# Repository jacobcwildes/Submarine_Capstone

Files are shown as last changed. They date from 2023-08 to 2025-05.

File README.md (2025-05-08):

# 2023 Submarine Capstone
This GitHub repo will go over the entire process of making a submersible ROV using custom PCBs, and almost entirely 3D printed hull pieces. This project was borne from ideas pooled by Dyllon Dunton and Jacob Wildes to fulfill a senior Capstone at the University of Maine. The end goal of this project is to have a submersible drone which can be operated by human input, and all relevent telemetry (i.e. forward velocity, and depth) will be displayed to the user. The bulk of the project was split into two parts: Dyllon Dunton completing the submarine portion and all PCB layouts, and Jacob Wildes completing the controller and all of the startup networking. Additionally, as Jacob progresses with his undergrad thesis work, eventually the need for human input will dwindle. Instead, a neural network will randomly patrol an area and as things appear (i.e. fish, lakegrass, etc.) that object will be outlined, and if desired, saved to local memory. By using IMU telemetry, the submarine should not continuously patrol the same route, though currents and other unconsidered elements may alter this. However, that is a non-issue because of the nature of the environment. Aquatic life is not constrained to the same location at all times, so even if it were in the same area twice, there may be something there that was not before.

# Photos



<div style="display: flex; gap: 10px;">
    
    
</div>

## Index
[STL Docs](https://github.com/jacobcwildes/Submarine_Capstone/tree/main/manufacturing_stls/README.md)

[PCB Docs](https://github.com/jacobcwildes/Submarine_Capstone/blob/main/pcb_files/README.md)

[Node Docs](https://github.com/jacobcwildes/Submarine_Capstone/tree/main/ros2_ws)

[STM Docs](https://github.com/jacobcwildes/Submarine_Capstone/tree/main/stm32_ws)

## Software Requirements
- Machine must be running Ubuntu 20.04.5 LTS
- ROS2 Foxy 
    - Can be installed using these [directions](https://docs.ros.org/en/foxy/Installation/Ubuntu-Install-Debians.html)
- CycloneDDS
    - Can be installed by doing the following: ```sudo apt install ros-foxy-rmw-cyclonedds-cpp```
    - This either needs to be sourced each time by running ```export RMW_IMPLEMENTATION=rmw_cyclonedds_cpp``` or automatically by adding it to the bashrc file.
- Docker Engine (optional - useful if a premade image is desired)
- OpenCV - the latest version is OK
    - Install can be found [here](https://docs.opencv.org/4.x/d7/d9f/tutorial_linux_install.html)
    - Note that Jacob highly recommends going directly to detailed install process. The quickstart makes it easy to make a mistake!
- Python 3.8.10
- Pyserial - latest version is OK. Can be installed with:
python3 -m pip install pyserial
 - STM32CubeMX or STM32CubeIDE
    - CubeMX is fine if you are comfortable with Makefiles. Otherwise, use the IDE which makes flashing the board as easy as pressing a play button 

## Hardware Requirements
- 2 Raspberry Pi 4Bs were used with 8 GB of RAM (one for the submarine, one for the controller). It may be possible to achieve success with less, but bear in mind there is much OpenCV work being done on the controller side to run the display.
- STM32 Nucleo-L4R5ZI (For submarine)
- STM32 Nucleo-L452RE-P (For controller)
## Installation

Since this is a large project, installs can sometimes get pretty messy. For example, ROS2 uses ```colcon build``` to prepare an executable. This is very handy and incredibly powerful. _However_ there isn't any sane way to rein in what colcon attemps to build, and surprise surprise, when colcon expects python and runs across C source code, it has no idea what to do. To alleviate this, we have made subdirectories called ros2_ws (which acts as our root ROS2 folder for all nodes) and stm32_ws (which acts as the root STM workspace for both the controller and submarine).

To actually download/install, follow these steps:

## Pi Setup

As per usual, it is never a super easy process to set anything up. To flash the Raspberry Pi Jacob opted to use the official [Raspberry Pi Imager](https://www.raspberrypi.com/software/). This tool allows for easy flashing of SD cards. However, when perusing the options to install the Ubuntu environment, as of the date of flashing (7/23), there was no 64-bit Ubuntu 20.04.5 LTS desktop option. The only option was a server version. Without much other option, the server option works as a good enough base. In Jacob's experience, even if a Wi-Fi setting is given in the imager, it still fails to find a network connection when the server is booted (note that the server version is only a command line). 

*NOTE*: For easiest plug and play ability, use the username "controller" for the controller and "ubuntu" for the submarine. If these are not followed, the systemd files will have to be modified so that the absolute paths line up. Systemd does not yet have access to the $USER environment variable so it cannot be flexible unfortunately.

In order to solve these networking woes, we need to modify our netplan file. This can be done by running 
```sudoedit /etc/netplan/<filename>.yaml``` 
where "filename" is the first entry that shows up when you hit tab a couple times. In Jacob's case it was 50-cloud-init.yaml, though your mileage may vary. 
Once inside the document, you will want to paste the following into it:
```bash

network:
    version: 2
    renderer: networkd
    ethernets:
        eth0:
            dhcp4: false
            critical: true #Tell netplan this is important and should be done early in setup
            addresses:
                - <your_desired_address>/24
    version: 2
    wifis:
        wlan0:
            optional: true
            access-points:
                <Wi-Fi_name>:
                    password: <your_password>
            dhcp4: true
            dhcp4-overrides:
                use-dns: false
            critical: true #Tell netplan this is important and should be done early in setup
            nameservers:
                addresses: [<Your ISP DNS here>] #Note this changes per ISP, can be easily looked up. Google also has development DNSes as well at 8.8.8.8 and 8.8.4.4
            routes:
                - to: 0.0.0.0/0 #All possible IPv4 addresses. Wildcard route for any unmatched traffic 
                  via: 192.168.1.1 #Gateway IP Address
                  metric: 100 #Give a priority. Lower metric means higher priority

```
"your_desired_address> should be something like 192.168.1.X, but it can be whatever you like. This makes it so when we attach both Pis together, they have a static IP and can immediately talk to each other. "Wi-Fi_name" is the name of your wireless network. "your_password" is the password of your wireless network. 

The eth0 option is needed because by default the Pi will not pick up the ethernet connection. This is probably because the gnome desktop is installed over top of the server installation, and the GUI functionality does not work.

Once that is done, it is time to apply those changes. Run the following:
```bash
sudo netplan generate && sudo netplan apply
```
This command will take some time, but afterward the Pi should be attached to the web!

## Getting the Ubuntu Desktop
Now that the Pi is on the web, it is important to actually get our GUI installed. To do so run the following:
```bash
sudo apt update && sudo apt upgrade -y
```
```bash
sudo apt install sudo apt install ubuntu-desktop -y && sudo reboot
```
Once the desktop is installed, you will be ready to download/run the nodes!

NOTICE: If you install SLiM, the boot process will be anywhere from 4-5 seconds faster. This also poses a risk of interfering with netplan since the GUI will also try to interface with wireless networks. Should you have installed SLiM, use the GUI to connect to Wi-Fi and comment out the wlan0 section of the netplan.

Note: This must be done twice, once for each Pi. Make very sure that the designated IP address for the eth0 port is not the same on both Pis! It absolutely will not work if both Pis have the same. 

## Software Install
1)
```bash
git clone https://github.com/jacobcwildes/Submarine_Capstone.git
```

3)
```bash
cd Submarine_Capstone/ros2_ws
```

4)
```bash
source /opt/ros/foxy/setup.bash
```

6) Note: **Before** running this step, make sure you are NOT in the ros2_ws/src directory. When colcon builds it makes 3 directories. An install, a build, and a log directory. When we go to run a ROS2 node, we first source the bash script in the install folder. The way Jacob has set up the launchfiles, the node WILL fail if the folders are not properly built.
```bash
colcon build
```

8) Once the build is finished
```bash
source install/setup.bash
```

## Creating a Mountpoint for the USB drive

First, make sure that the USB drive you are trying to flash is in FAT32 type. It can be any size as we are only saving desired screenshots to the drive. Once it is formatted (if necessary at all), plug into the Pi and do the following:

1)
```bash
sudo fdisk -l
```
Find the drive that corresponds to your drive. I found it is easiest to identify by size and type. If you know it is FAT32 and is 16GB in size, you can deduce the device mountpoint. In our case, it was "/dev/sdb1"

2) Next we need to get the UUID of the drive by running the following:
```bash
sudo ls -l /dev/disk/by-uuid/
```
Look for the entry that corresponds to your mountpoint. For example, our UUID was "A097-2639"

3) Now we need to make a folder for the USB to mount to
```bash
sudo mkdir /mnt/usb
```
The folder name can be whatever you want, but for simplicity I went with "usb"

4) Now we're going to modify the fstab file so that the drive will _always_ be mounted to the "/mnt/usb" partition
```bash
sudo nano /etc/fstab
```

5) Add the following line to the end
```bash
UUID=A097-2639 /mnt/usb vfat uid=${USER},gid={USER} 0 0
```
UUID is your drive ID, and ${USER} is your system username. 

6) Reboot or immediately test by running:
```bash
sudo mount -a
```
If all went well, the drive will be mounted to "/mnt/usb"!
## Flashing STM Boards

_Installing with STM32CubeIDE_

First, make sure that the IDE is installed on your computer. It can be installed from [STM's website](https://www.st.com/en/development-tools/stm32cubeide.html).
Once the software is installed, open the IDE and navigate first to the controller_stm.ioc which can be found in ```Submarine_Capstone/stm32_ws/controller_stm```. Once the project is open in the IDE, the next step is to press the green play button on the top of the screen to flash the Nucleo-L452RE-P with the controller program as shown below
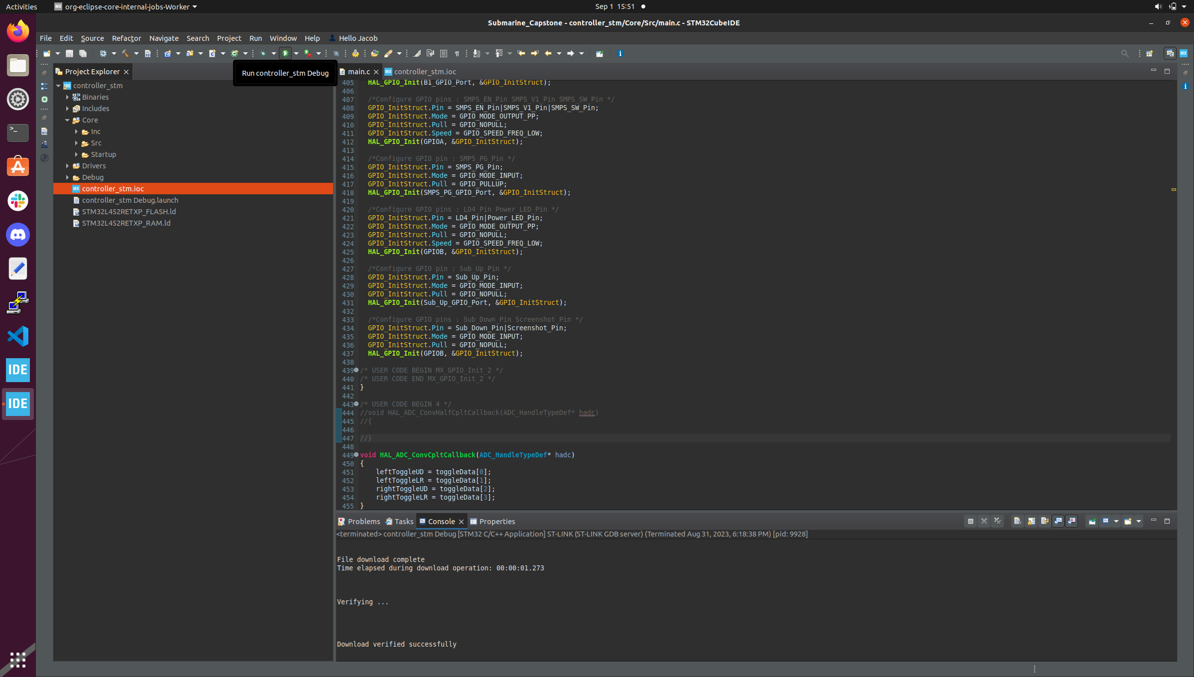
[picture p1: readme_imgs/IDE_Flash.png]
STM32CubeIDE Steps


You will know when the program flashes when the LED next to the USB connection illuminates green.

Repeat this step for the submarine by navigating to ```Submarine_Capstone/stm32_ws/submarine_stm/Submarine_MicroController```

_Installing with STM32CubeMX_

Installing with the CubeMX is a little bit different than the IDE - it is significantly more involved, but for some is the preferred method (especially if your device does not support the IDE). 

First, make sure that you have arm-none-eabi installed on your system. This step can be an absolute nuisance, so the steps are listed below:

1) Check to make sure that you don't have any arm libraries lurking that could foul the download:
```bash
sudo apt remove gcc-arm-none-eabi
```
2) Download the [arm-none-eabi-gcc tarball](https://developer.arm.com/downloads/-/gnu-rm). Note this guide is specifically for Linux. MacOS and Windows mileage will vary from this  guide.

3) Unpack the tarball into some sort of directory. In this case we arbitrarily chose /usr/share
```bash
sudo tar xjf gcc-arm-none-eabi-YOUR-VERSION.bz2 -C /usr/share/
```
"YOUR-VERSION" is whatever version ARM happens to have released at the time

4) Create symlinks from the install folder to the /usr/bin folder like so:
```bash
sudo ln -s /usr/share/gcc-arm-none-eabi-YOUR-VERSION/bin/arm-none-eabi-gcc /usr/bin/arm-none-eabi-gcc 
sudo ln -s /usr/share/gcc-arm-none-eabi-YOUR-VERSION/bin/arm-none-eabi-g++ /usr/bin/arm-none-eabi-g++
sudo ln -s /usr/share/gcc-arm-none-eabi-YOUR-VERSION/bin/arm-none-eabi-gdb /usr/bin/arm-none-eabi-gdb
sudo ln -s /usr/share/gcc-arm-none-eabi-YOUR-VERSION/bin/arm-none-eabi-size /usr/bin/arm-none-eabi-size
sudo ln -s /usr/share/gcc-arm-none-eabi-YOUR-VERSION/bin/arm-none-eabi-objcopy /usr/bin/arm-none-eabi-objcopy
```
Note: These symlinks may or may not be necessary. On some systems Jacob has worked with, the symlinks were a problem. In other systems, they were not. For safety's sake it's easy enough to just create them and prevent headache later.

5) ARM in its infinite wisdom does not give all the necessary dependencies in its README.txt, but these dependencies served well for this project:
```bash
sudo apt install libncurses-dev
sudo ln -s /usr/lib/x86_64-linux-gnu/libncurses.so.6 /usr/lib/x86_64-linux-gnu/libncurses.so.5
sudo ln -s /usr/lib/x86_64-linux-gnu/libtinfo.so.6 /usr/lib/x86_64-linux-gnu/libtinfo.so.5
```
Note: The libncurses.so.6/.so.5 may not be the same at a later date.

6) Check to make sure that the arm-none-eabi was properly installed:
```bash
arm-none-eabi-gcc --version
arm-none-eabi-g++ --version
arm-none-eabi-gdb --version
arm-none-eabi-size --version
```
Make should be installed on your system since OpenCV is a prerequisite for this system to work, but just in case it isn't:
```bash
sudo apt update && sudo apt install make
```
Next, navigate to ```Submarine_Capstone/stm32_ws/submarine_stm/Submarine_MicroController```. This is where the Makefile is.
Run
```bash
make -j4
```
Once the build is complete, run the following:
```bash
cp BINARY_PATH /media/${USER}/BOARD_NAME/
```
BINARY_PATH will be filled in soon, BOARD_NAME is the name of the board when it is plugged into the computer.

If all worked well, the board will be successfully flashed!

Thankfully, once a board is flashed it stays flashed. Once the board is powered, it will immediately begin whatever program is on it.

## Setting up ROS2 to run on boot
This step took a huge amount of debug. Crontab does not play well with ROS2, so Jacob had to opt for systemd instead. Within the Submarine_Capstone/ros2_ws/Netplan_Init directory, there are four netplan service files. Two for the submarine, two for the controller. These must both be copied to the ```/etc/systemd/system/``` directory. To be clear, submarine service files go in the submarine Pi systemd directory, and the controller files go in the controller Pi systemd directory.

_*NOTE*_ If the username convention was not followed at the beginning, you will need to go into each of the four service files and change everywhere it says "controller" or "ubuntu" with your respective username otherwise the pathing will NOT work.

1) Copy the files:
```bash
cd Submarine_Capstone/ros2_ws/Netplan_Init && sudo cp <one_of_four.service> /etc/systemd/system/
```

2) Enable the systemd services:
```bash
sudo systemctl enable <one_of_four.service>
```

3) Start the systemd services:
```bash
sudo systemctl start <one_of_four.service>
```

4) Check the service status:
```bash
sudo systemctl status <one_of_four.service>
```

5) Change permissions for the init scripts. This is potentially pretty security breaking, but after setup these pis should never see the web again, so a risk that is acceptable
```bash
sudo visudo
```
Add the following lines to the ```User privilege specification``` section:
```bash
<username> ALL=(ALL) NOPASSWD: /home/$USER/Submarine_Capstone/ros2_ws/Netplan_Init/netplan_init.sh
<username> ALL=(ALL) NOPASSWD: ALL
<username> ALL=(ALL) NOPASSWD: /usr/sbin/netplan apply, /bin/ping
<username> ALL=(ALL) NOPASSWD: /usr/sbin/netplan generate
<username> ALL=(ALL) NOPASSWD: /bin/systemctl start netplan-ovs-cleanup.service, /bin/systemctl stop netplan-ovs-cleanup.service
```
ALL=(ALL) In this sudoers file grants all users the ability to execute any command as any user or group using ```sudo``` without a password. Again, huge security risk but since there will only be one account on these devices which after setup will not be on a network, this risk is acceptable.

6) Enable the following to make sure that networkd will operate
```bash
sudo systemctl enable systemd-networkd
sudo systemctl enable systemd-resolved
```
Remember! These steps must be done twice, once for the controller, once for the submarine!

## Making the controller properly launch
After some more testing, it became apparent that systemd struggles immensely to bring the display online. This is so much so that it causes the GUI to fail. To remedy this, we will utilize Ubuntu Desktop's clever feature - autologin and run on login. This step does require that GNOME is installed, instead of SLiM. To make this work run the following:

1) Set up autologin directory:
```bash
mkdir -p ~/.config/autostart
```

2) Create an autorun script:
```bash
gedit ~/.config/autostart/controller_launch.desktop
```

3) Add the following to the script:
```bash
[Desktop Entry]
Type=Application
Exec=/home/controller/Submarine_Capstone/start/controller_start.sh
Hidden=false
NoDisplay=false
X-GNOME-Autostart-enabled=true
Name=controller_launch
Comment=Launch_Controller_After_Login
```

4) Make the script executable
```bash
sudo chmod +x ~/.config/autostart/controller_start.sh
```

On next login the GUI will launch!

_Note_: The ```.desktop``` script asssumes that the controller Pi has the username ```controller```. If that is not the case, swap the name in the path for the proper name.

## Docker
If these installation steps sound gross, no sweat! Jacob has made a docker image which is able to run on just about any 64 bit version of Linux. MacOS and Windows may be compatible, but are untested. In order to use the provided images, do the following:

1) Clone this repo
```bash
git clone https://github.com/jacobcwildes/Submarine_Capstone.git
```

3) Pull the images down from Docker Hub:
```bash
docker pull jacobcwildes/2023-submarine-capstone:controller-deploy
```

```bash
docker pull jacobcwildes/2023-submarine-capstone:submarine-deploy
```

These downloads will take a little time, as they are both between 1 and 1.6 GB. 

Alternatively, if you desire to build the Docker images locally, repeat step 1 and pull this repo.

Then do the following:

1) This is where the Dockerfiles are.
```bash
 cd Submarine_Capstone/ros2_ws
```

2)
  Build the Controller Docker image (Note that this will take a long time - it must download everything from the Ubuntu:20.04.5 base)
```bash
docker build -t controller_image . < controller_Dockerfile
```

4) Build the Submarine Docker image:
```bash
docker build -t controller_image . < sub_Dockerfile
```

Once the builds are complete, the launch sequence is the same for both methods of installation.  Simply run:

For the controller:
```bash
docker compose -f controller_compose.yaml up
```
For the submarine:
```bash
docker compose -f sub_compose.yaml up
```

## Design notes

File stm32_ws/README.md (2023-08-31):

# STM Board Decisionmaking

Since the project is entirely self contained, power is a concern. That being said, we knew that we needed as much power efficiency as possible. According to [Digi-Key's](https://www.digikey.com/en/maker/blogs/2020/understanding-stm32-naming-conventions) website, the flag after "STM" is the type. We opted for two low power boards. 

As far as the controller STM board is concerned, there are not many things that need to be driven or read from. There is only one button for a screenshot, a switch to control up/down, and 4 ADC channels. That being the case,
we opted for the STM32-L452RE-P. This was primarily because it was already on hand from a previous class, and met the criteria of being low power. 

Had we not had that board on hand, a good alternative would have been the [Nucleo-L432KC](https://www.st.com/en/evaluation-tools/nucleo-l432kc.html#st_all-features_sec-nav-tab) as it still has the same functionality, is still low power, but has even fewer wasted pins than on the currently selected board.

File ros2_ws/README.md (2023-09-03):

# ROS2 Decisionmaking
There are multiple ways to have made this project.  A perfectly viable way would have been back and forth serial transmission of commands from controller to submarine and then a faster ethernet wire for image transfer. However, that is not particularly sustainable or easily scalable. If I wanted to have multiple separate modules receive data, I would have to have some sort of way to pass that same data to multiple recipients. That would require more hardware or a more complex software side to make sure this is accomplished well. 

A prime example of this issue is my (Jacob's) extension into the thesis. I want another (much more powerful computer than Raspberry Pi) to also receive image data from the camera and then pass that along to the controller to display. If I were not to use ROS2, this process would be much less straightforward. I would have to pipe data from the camera to the external computer for interpretation and then to the controller. Then what happens if something goes wrong with the external computer? The camera feed would die and then the sub would be at some unknown point because the operator has just lost visual with it. 

This is the beauty of ROS2. Instead of being direct connections to everything (i.e. Bill talks to Bob and **only** to Bob), Bill is on a loudspeaker and anyone who wants to listen (in ROS2 terminology, subscribe) can. It does not impact publication speed, the only difference is that multiple things can subscribe and receive data all at once. Now Bill can talk to Bob, Frank, and Mary all at once and there isn't the software/hardware equivalent of a tin can on a string so that everyone gets the information.

Before there are woes and worries about specific TCP/UDP settings, ROS2 offers something called Quality of Service (QoS) settings which allows the programmer to explicitly tell ROS that if a message is published and someone is subscribed, they absolutely have to receive and acknowledge that message before anything else is done. ROS2 can be as "reliable" as TCP or as "best-effort" as UDP. The only requirement is that both subscriber and publisher have this table of settings: 

| Publisher | Subscriber  | Compatible |
|---|---|---|
| Best effort  | Best effort | Yes |
| Best effort  | Reliable | No |
| Reliable | Best effort | Yes |
| Reliable | Reliable | Yes |

The only scenario where the publisher and subscriber types are incompatible are when the subscriber is expecting a reliable (TCP) connection, but instead receives a best effort (UDP) connection. Unlike TCP, UDP does not acknowledge a verification packet to have a sort of "handshake" agreement. Without that handshake, the subscriber has no idea that it is supposed to be receiving, and therefore will not connect. The same is true here in the ROS2 QoS ecosystem. According to the documentation, if the publisher is configured to be reliable, it may attempt multiple times to transmit each message being published to the reliable subscriber. That of course, depends on another configuration, like history, or keep all options. That allows the publisher to cache all unreceived messages to continuously try and hail the subscriber.

The official documentation on ROS2 QoS can be found [here](https://docs.ros.org/en/rolling/Concepts/Intermediate/About-Quality-of-Service-Settings.html)

In addition to this rather compelling reason, ROS2 is the de facto foundation for robotics. When I began my first internship at UMaine, one of the first things that I was introduced to was ROS2. It allows for fast scalability and it is generally stable. If that isn't extra reason enough, during my time at the ASCC, all of the projects I have been apart of have been built on the back of ROS2 Foxy.

There are two final questions to answer. Why in particular ROS2 Foxy? Why ROS2 over ROS1?

There are multipe releases of ROS2. Each adds some functionality or other, but they are undeveloped at the inital release. There are multiple bugs that aren't found immediately, and some are on more recent releases of Ubuntu. Although Ubuntu 20.04.5 LTS is reaching the end of its lifespan (as of August of 2023), it has been around long enough that multiple security patches have been released, and there are a whole host of development libraries that have been released for it already - some that may or may not be available to newer versions. ROS2 Foxy has also reached the end of its lifespan, but since it has been around for a long time, it has sort of become the Windows 7 of ROS2. It is wildly popular among development groups because there have been so many patches released and packages made specifically for Foxy that it is hard to move on to a newer version where those packages may break.

To answer the final question, ROS1 **only** supports TCP connections. That would put an additional strain on the system to try to receive every single frame from the camera. If a couple of frames are dropped here or there, not a big deal. It would be more taxing to constantly grab every single frame than it would be to take whatever can be grabbed by the program.

## Node Structure
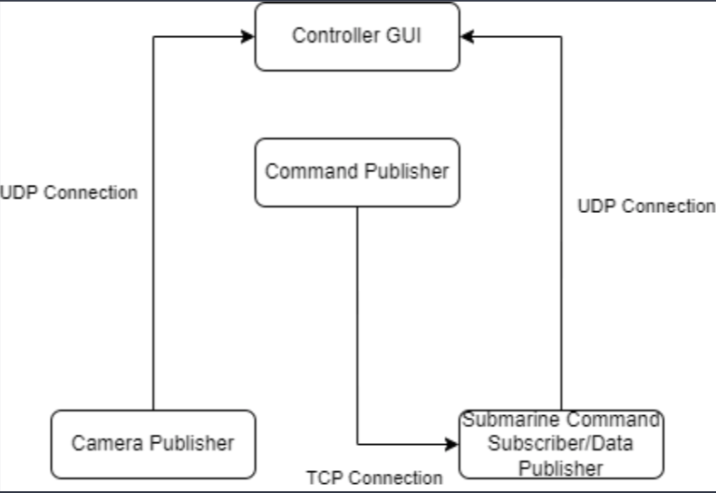
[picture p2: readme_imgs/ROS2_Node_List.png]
ROS2 Node Structure


## Why CycloneDDS and what is it?

[CycloneDDS](https://github.com/eclipse-cyclonedds/cyclonedds#what-is-dds) is a very cool system. Basically, DDS is used in a huge variety of distributed systems (which if you aren't sure what a distributed system is, it's a netowrk of independent components that communicate together to acheive a common goal) from railway controls, medical systems, to smart greenhouses. The beauty of CycloneDDS is that it is built entirely in open source. Anyone is free to poke around all the inner workings as compared to a close relative, [OMG DDS](https://www.omg.org/spec/DDS/1.4/About-DDS/).

As for why CycloneDDS was chosen, it is very popular in robotics and autonomous vehicales because of their dependency on high-throughput, low-latency control systems without having a single point of failure by the message broker. In addition, it is used by default as the middleware for ROS2 (another implicit reason to use it!)

Since CycloneDDS is an open source version of OMG DDS, it follows the same following specifications:
- Structural type definition to allow automatic endianness conversion
- Type checking between readers and writers
- Support for type evolution

There are a whole host of other specifications that can be found both at the previously linked OMG DDS and CycloneDDS links.

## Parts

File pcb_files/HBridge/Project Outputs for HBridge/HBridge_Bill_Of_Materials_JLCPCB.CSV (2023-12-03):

Comment | Designator | Footprint | Part num
Screw Terminal Header, 2-pin | J1 | PHOENIX_1935776 | 1935776
Screw Terminal Header, 2-pin | J2 | PHOENIX_1935776 | 1935776
Screw Terminal Header, 2-pin | J3 | PHOENIX_1935776 | 1935776
Screw Terminal Header, 2-pin | J4 | PHOENIX_1935776 | 1935776
Screw Terminal Header, 2-pin | J5 | PHOENIX_1935776 | 1935776
Screw Terminal Header, 2-pin | J6 | PHOENIX_1935776 | 1935776
Screw Terminal Header, 2-pin | J7 | PHOENIX_1935776 | 1935776
Capacitor | C10 | C1210 | 1210Y0500104KST
Capacitor | C15 | C1210 | 1210Y0500104KST
Capacitor | C5 | C1210 | 1210Y0500104KST
Resistor | R3 | RESC5025X70N | 35021R5FT
Resistor | R4 | RESC5025X70N | 35021R5FT
Capacitor | C1 | C1210 | C1210C104J5RAC7800
Capacitor | C11 | C1210 | C1210C104J5RAC7800
Capacitor | C13 | C1210 | C1210C104J5RAC7800
Capacitor | C3 | C1210 | C1210C104J5RAC7800
Capacitor | C6 | C1210 | C1210C104J5RAC7800
Capacitor | C8 | C1210 | C1210C104J5RAC7800
Resistor | R10 | RESC3126X65N | CRGP1210F1M0
Resistor | R2 | RESC3126X65N | CRGP1210F1M0
Resistor | R6 | RESC3126X65N | CRGP1210F1M0
45-V, 2.5-A bipolar stepper or dual H-bridge motor driver IC with current regulation and PWM control | U1 | IC_TPS61196PWPRQ1 | DRV8841PWP
45-V, 2.5-A bipolar stepper or dual H-bridge motor driver IC with current regulation and PWM control | U2 | IC_TPS61196PWPRQ1 | DRV8841PWP
45-V, 2.5-A bipolar stepper or dual H-bridge motor driver IC with current regulation and PWM control | U3 | IC_TPS61196PWPRQ1 | DRV8841PWP
Resistor | R11 | RES_ERJ14RQJ1R0U | ERJ-14RQJ1R0U
Resistor | R12 | RES_ERJ14RQJ1R0U | ERJ-14RQJ1R0U
Resistor | R7 | RES_ERJ14RQJ1R0U | ERJ-14RQJ1R0U
Resistor | R8 | RES_ERJ14RQJ1R0U | ERJ-14RQJ1R0U
Capacitor | C12 | C1210 | KGM32LR51E476MU
Capacitor | C2 | C1210 | KGM32LR51E476MU
Capacitor | C7 | C1210 | KGM32LR51E476MU
Capacitor | C14 | C1210 | KGM32LR72A474KU
Capacitor | C4 | C1210 | KGM32LR72A474KU
Capacitor | C9 | C1210 | KGM32LR72A474KU
Resistor | R1 | RESC3126X65N | RC1210JR-0710KL
Resistor | R5 | RESC3126X65N | RC1210JR-0710KL
Resistor | R9 | RESC3126X65N | RC1210JR-0710KL

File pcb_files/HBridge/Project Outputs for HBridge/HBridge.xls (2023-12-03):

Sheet: BOM Report
Bill of Materials |  |  | Bill of Materials For PCB Document [HBridge.PcbDoc]
Source Data From: |  | HBridge.PcbDoc
Project: |  | HBridge.PrjPcb
Variant: |  | None
Creation Date: | 7/20/2023 | 1:09:59 PM
Print Date: | 45127 | 45127.5487
#Column Name Error:Footprint | #Column Name Error:Comment | #Column Name Error:LibRef | Designator | Description | Quantity
 |  |  | P6, P7, P8, P9 | Header, 3-Pin | 4
 |  |  | J5 |  | 1
 |  |  | J1 |  | 1
 |  |  | J3 |  | 1
 |  |  | J6 |  | 1
 |  |  | J7 |  | 1
 |  |  | J4 |  | 1
 |  |  | P3 | Header, 4-Pin | 1
 |  |  | P10 | Header, 4-Pin | 1
 |  |  | P13 | Header, 4-Pin | 1
 |  |  | P2 | Header, 4-Pin | 1
 |  |  | P5 | Header, 4-Pin | 1
 |  |  | P12 | Header, 4-Pin | 1
 |  |  | P1 | Header, 4-Pin | 1
 |  |  | R1, R5, R9 | 523 Ohms Â±1% 0.5W, 1/2W Chip Resistor 1210 _3225 Metric_ Moisture Resistant Thick Film | 3
 |  |  | P4 | Header, 4-Pin | 1
 |  |  | P11 | Header, 4-Pin | 1
 |  |  | U1, U2, U3 | 45-V, 2.5-A bipolar stepper or dual H-bridge motor driver IC with current regulation and PWM control | 3
 |  |  | R2, R6, R10 | 523 Ohms Â±1% 0.5W, 1/2W Chip Resistor 1210 _3225 Metric_ Moisture Resistant Thick Film | 3
 |  |  | R7, R8, R11, R12 | Resistor | 4
 |  |  | R3, R4 | Resistor | 2
 |  |  | C1, C2, C3, C4, C5, C6, C7, C8, C9, C10, C11, C12, C13, C14, C15 | Capacitor | 15
 |  |  | J2 |  | 1
 |  |  |  |  | 50
Approved |  | Notes

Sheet: Project Information
Project Full Path | C:\Users\dunto\Documents\sTUFF\School\Classes\Class Documents\2023Summer\Projects\HBridge\HBridge.PrjPcb
Project Filename | HBridge.PrjPcb
Variant Name | None
Data-Source Filename | HBridge.PcbDoc
Data-Source Full Path | C:\Users\dunto\Documents\sTUFF\School\Classes\Class Documents\2023Summer\Projects\HBridge\HBridge.PcbDoc
Title | Bill of Materials For PCB Document [HBridge.PcbDoc]
Total Quantity | 50
Report Time | 1:09:59 PM
Report Date | 7/20/2023
Report Date & Tine | 7/20/2023 1:09:59 PM
Output Name | Bill of Materials
Output Type | BOM_PartType
Output Generator Name | BOM
Output Generator Description | Bill of Materials

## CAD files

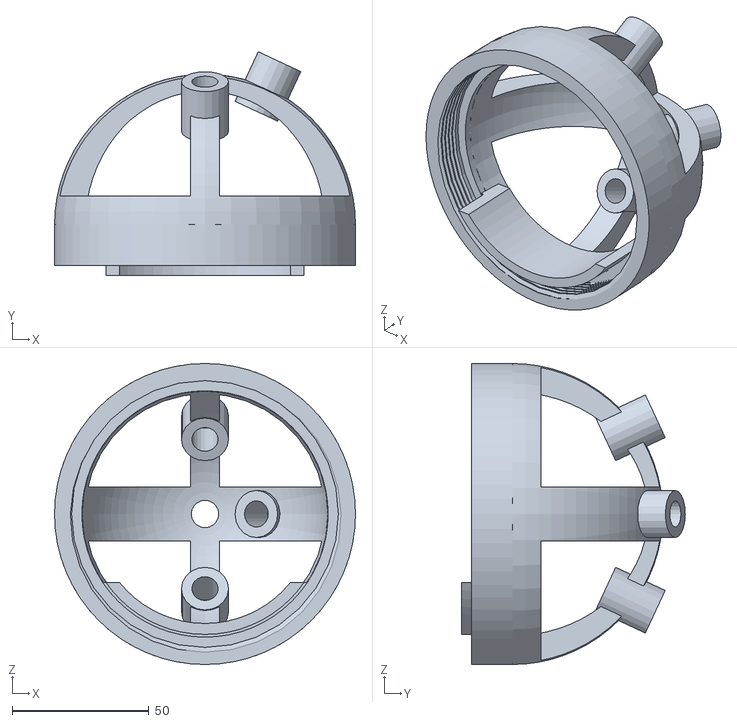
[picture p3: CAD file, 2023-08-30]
manufacturing_stls/Secondary_Dome_Left.stl
110.0 x 81.7 x 110.0

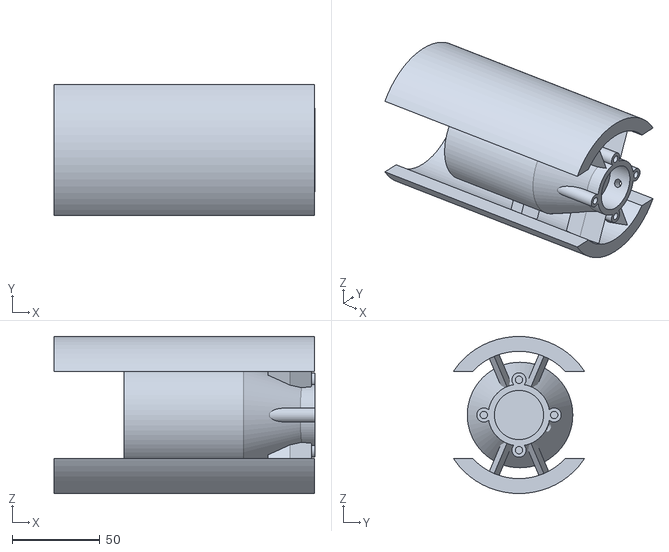
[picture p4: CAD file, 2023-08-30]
manufacturing_stls/Balast_Left.stl
148.3 x 74.5 x 89.3

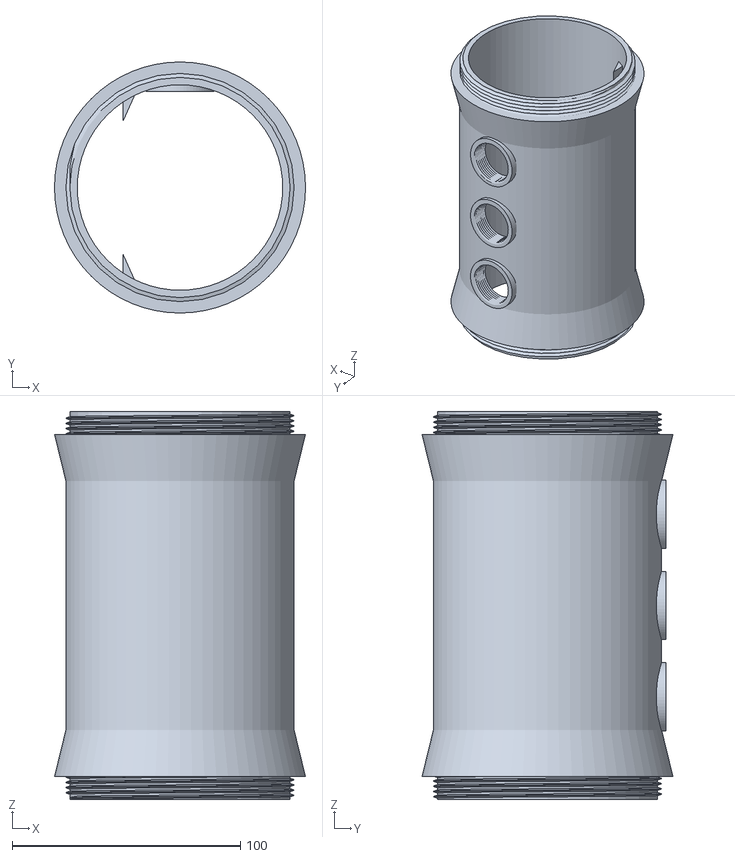
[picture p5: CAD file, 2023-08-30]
manufacturing_stls/Secondary_Hull.stl
110.0 x 110.0 x 170.0

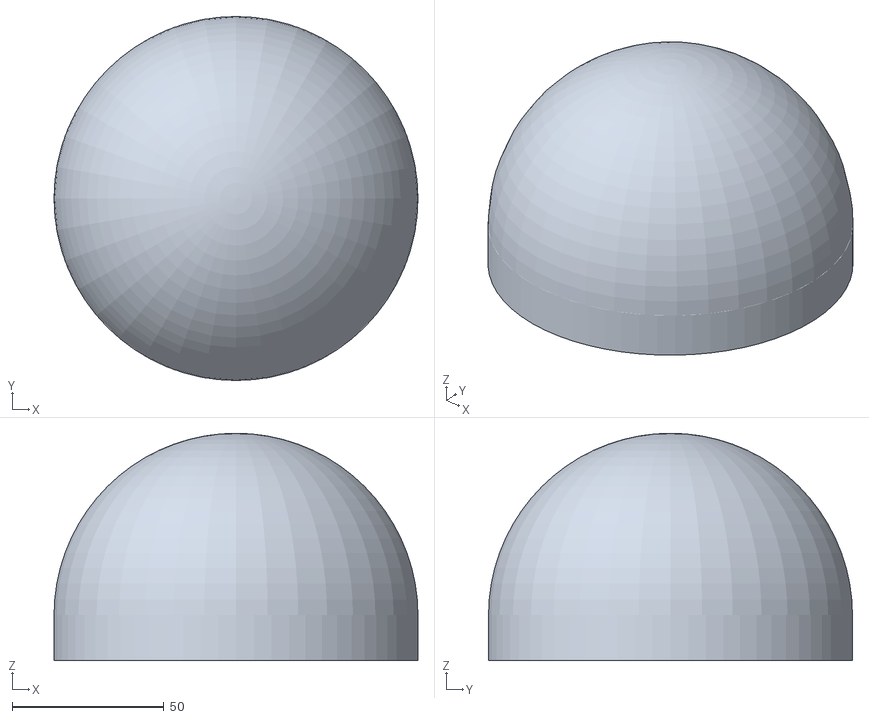
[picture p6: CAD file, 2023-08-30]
manufacturing_stls/Primary_Dome.stl
120.0 x 120.0 x 75.0

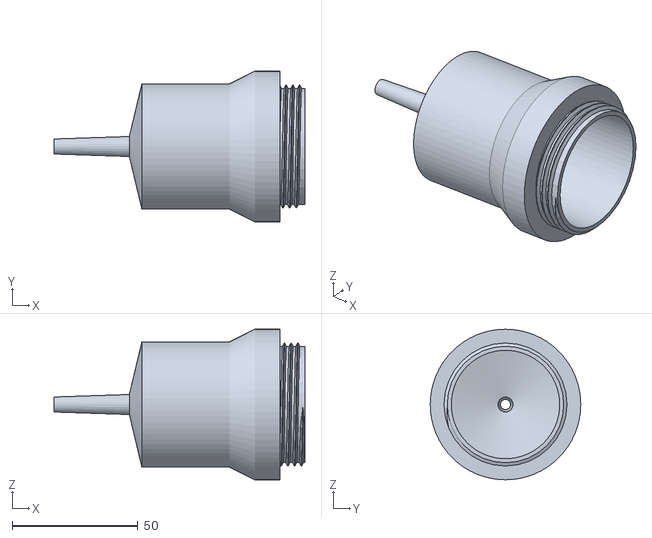
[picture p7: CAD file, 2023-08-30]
manufacturing_stls/Plunger_Right.stl
100.0 x 60.0 x 60.0

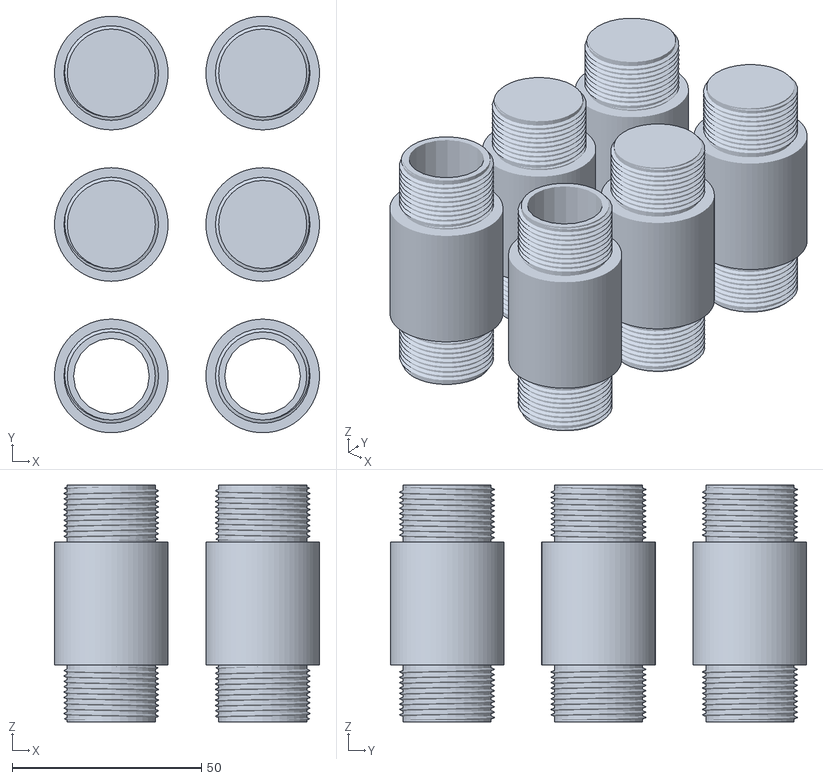
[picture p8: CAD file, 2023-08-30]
manufacturing_stls/Threaded_Rods_final.stl
70.0 x 110.0 x 62.5

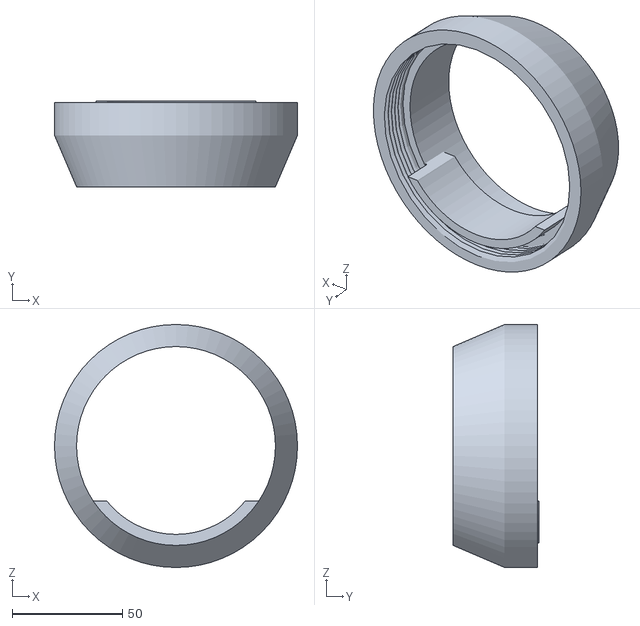
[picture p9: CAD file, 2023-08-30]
manufacturing_stls/Secondary_Cap.stl
110.0 x 39.0 x 110.0

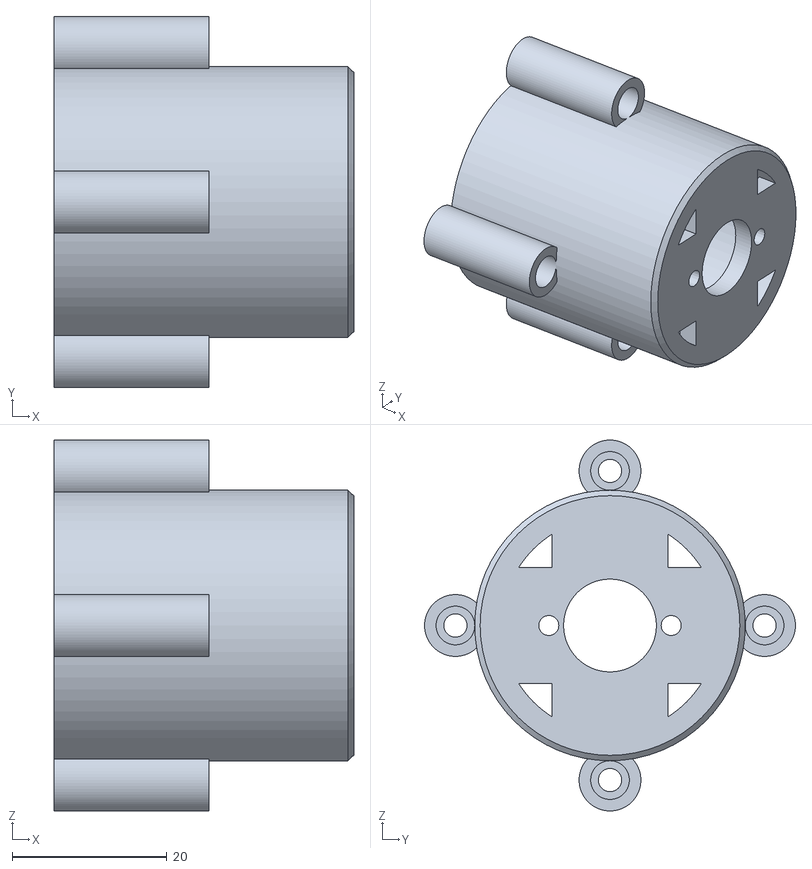
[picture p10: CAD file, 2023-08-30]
manufacturing_stls/Prop_Housing.stl
38.7 x 48.0 x 48.0

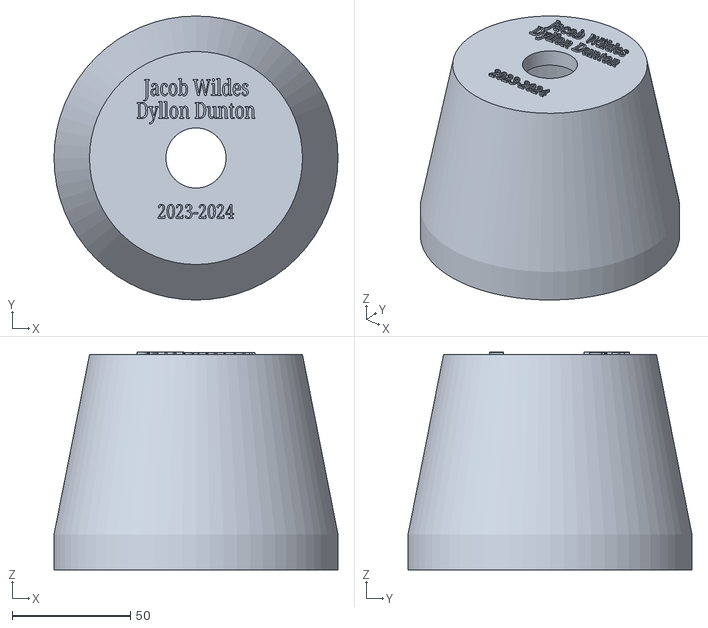
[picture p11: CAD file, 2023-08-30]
manufacturing_stls/BackCap.stl
120.0 x 120.0 x 92.0

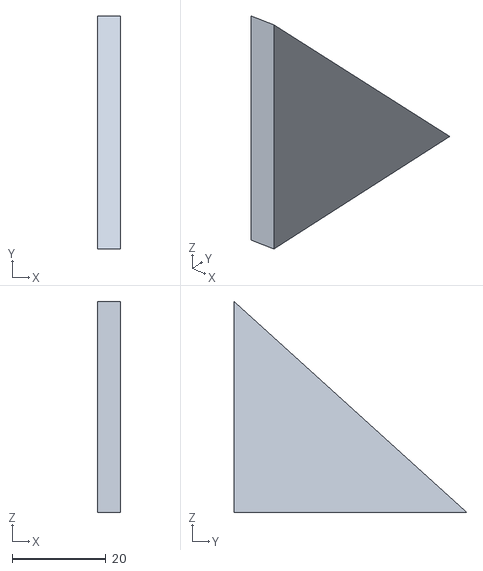
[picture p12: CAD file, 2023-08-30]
manufacturing_stls/Fin.stl
5.00 x 49.7 x 45.0

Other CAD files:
manufacturing_stls/Plunger_Left.stl
manufacturing_stls/Secondary_Dome_Right.stl
manufacturing_stls/Balast_Right.stl

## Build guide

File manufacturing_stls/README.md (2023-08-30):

## Printing Thought Process
Dyllon and I decided to try and manufacture everything ourselves as much as possible. This meant doing a lot of research on how best to manufacture because water is an unforgiving environment and we don't need to destroy our equipment while trying to use it for the intended purpose. 

That being said, there are 2 primary methods of 3D printing. FDM and SLA printing. FDM is much more common - and it is the de facto method as well. This involves extruding heated PLA, ABS, or other solid materials onto a heated bed. This is a great method for rapid prototyping as it is easy to postprocess and generally tends to print quickly SLA printing is a little more involved. For starters, SLA involves photopolymer resin and an LCD screen to cure. This allows very tight tolerances on prints, but the print process is much longer. Most notably, the post-processing task is very involved. Once the print is done, the operator has to first and foremost wear safety glasses, gloves, and a breathing mask because of the toxic nature of photopolymer resin. Then the print must be removed from the printer and placed in an isopropyl alcohol bath which can take anywhere from 30 seconds to 10 minutes. I opted to keep the wash time low, but that is mostly because there is a fine line to walk between washing it so much that the process time is even longer because the excess IPA has to dry, and not rinsing the excess resin off before trimming supports and curing. 

Although it sounds like FDM printing is the way to go in this case, take note that layer lines are a big deal in this application. On FDM printers you can almost see each layer line (obviously depending on what size nozzle is used). However, in SLA printing the layer lines are significantly smaller. As in, anywhere from 25 to 100 microns. This is very important for keeping water out. A quick Reddit scour shows that when folks print with FDM for water retention purposes, one of the first failure points is the layer line. Having such a small layer line on an SLA print makes this a much smaller likelihood. Additionally, SLA allows for clear and translucent prints, which is important where the entire robot is custom designed and built. There aren't any prebuilt observation domes. That had to be built by us as well.

This is all to say we opted for SLA printing even though it is a more involved process simply because the end product is likely to be of higher quality, and the robust nature of cured photopolymer resin is desirable over FDM. 
## Software
Just like in FDM printing, a slicer and modeler is required. For simplicity, Dyllon and I used [tinkerCAD](https://www.tinkercad.com/login) to model each individual component. Although there is a whole slew of more powerful modeling softwares out there like Blender, tinkerCAD has the smallest learning curve, and for our purposes works just fine. 

As slicers are concernced, I opted to use what Elegoo recommends, which is [ChituBOX](https://www.chitubox.com/en/index). Some folks use others, but as an entrance into SLA printing this software works fine and had a shallow learning curve.
## Materials and Equipment Used
Since Dyllon and I are really wanting this to be something people can build or modify at home, I think it is important to list basically everything we used. 

Equipment:
- [Elegoo Saturn 2 8K](https://www.elegoo.com/products/elegoo-saturn-2-8k-10-inches-mono-lcd-3d-printer)
- [Elegoo Wash/Cure Station](https://www.elegoo.com/products/elegoo-mercury-x-bundle-washing-and-curing-machine)
- Rubber Gloves (disposable latex gloves are also fine)
- Safety Glasses (It is very easy for IPA or rogue splintering pieces to find their way into your unprotected eyes - ask me how I know)
- Sanding Paper 
     - This is an essential post processing step for clear resins. In my experience thus far I recommend grits from 120-10,000. This allows us to really work out any imperfections in the print and especially make the dome clear like glass.

Materials:
- [Elegoo Translucent Resin](https://www.amazon.com/dp/B07Z994PW2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) Elegoo has been making resin for a long time. Their formula is pretty tried and true, and even if you don't have your slicer settings completely dialed in it still tends to yield pretty fair results.
     - I recommend about 5-7 kilograms of this resin because it comprises almost the entire hull (and it is good to account for any mistakes, trust me I made many whilst printing)
     - It is not entirely necessary that translucent resin be used for the hull or connectors. Those can be any color you like! Dyllon and I just wanted to be able to see all of the internals as well.
- [Siraya Tech Resin](https://www.amazon.com/Siraya-Tech-Ultra-Clear-Non-Yellow-Transparency/dp/B09LQW7RHX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) 
     - This resin yielded a very clear observation dome. There may be better alternatives out there, but this more than does the job.
     - I recommend 1 kilogram of the stuff unless you want to make more components clear. Do note that this resin is a bit harder to use than Elegoo, so if you are not entirely confident in your SLA printing skills consider opting for an alternative. 
## Post-Processing
Please note that while I do have *some* eperience with SLA 3D printing, I am by no means an expert. Some of my processes may look extremely barbaric to those who are more well versed, but the outcome was of at least acceptable quality. 

I found that anywhere from 30 seconds to 2 minutes was sufficient to wash the excess resin off.

Next comes trimming supports. There isn't a particular time frame with this, the only advice I can offer is to take things extrememly slowly. Resin is generally stronger after being cured, but where it hasn't been fully cured yet, it is prone to chipping off. This is especially true near the connection point between supports and the actual print.

Finally, curing is necessary. For the curing machine that I listed, I like to insert the model for 30 seconds each time. You can tell when it is cured because it will not be tacky to the touch. If it is, hit it with another 30 seconds. The curing machine could be set to more time, but it is very important not to overexpose the translucent or clear resins, as they will begin to turn yellow. 

Once these steps are complete and all parts are printed, I recommend going to the local hardware store or Home Depot and picking up some clear resin/polyurethane. Make sure it is flat/low gloss just to make sure there isn't any undesired shine bouncing back into the camera. The poly/clear resin is a good final coat to fill in any minor imperfections in the print and further reduce the likelihood of a leak through the hull. Do not be bashful with the application of the exterior coats, the more the merrier. If it accidentally dries globbed, just sand off the mistake and reapply.

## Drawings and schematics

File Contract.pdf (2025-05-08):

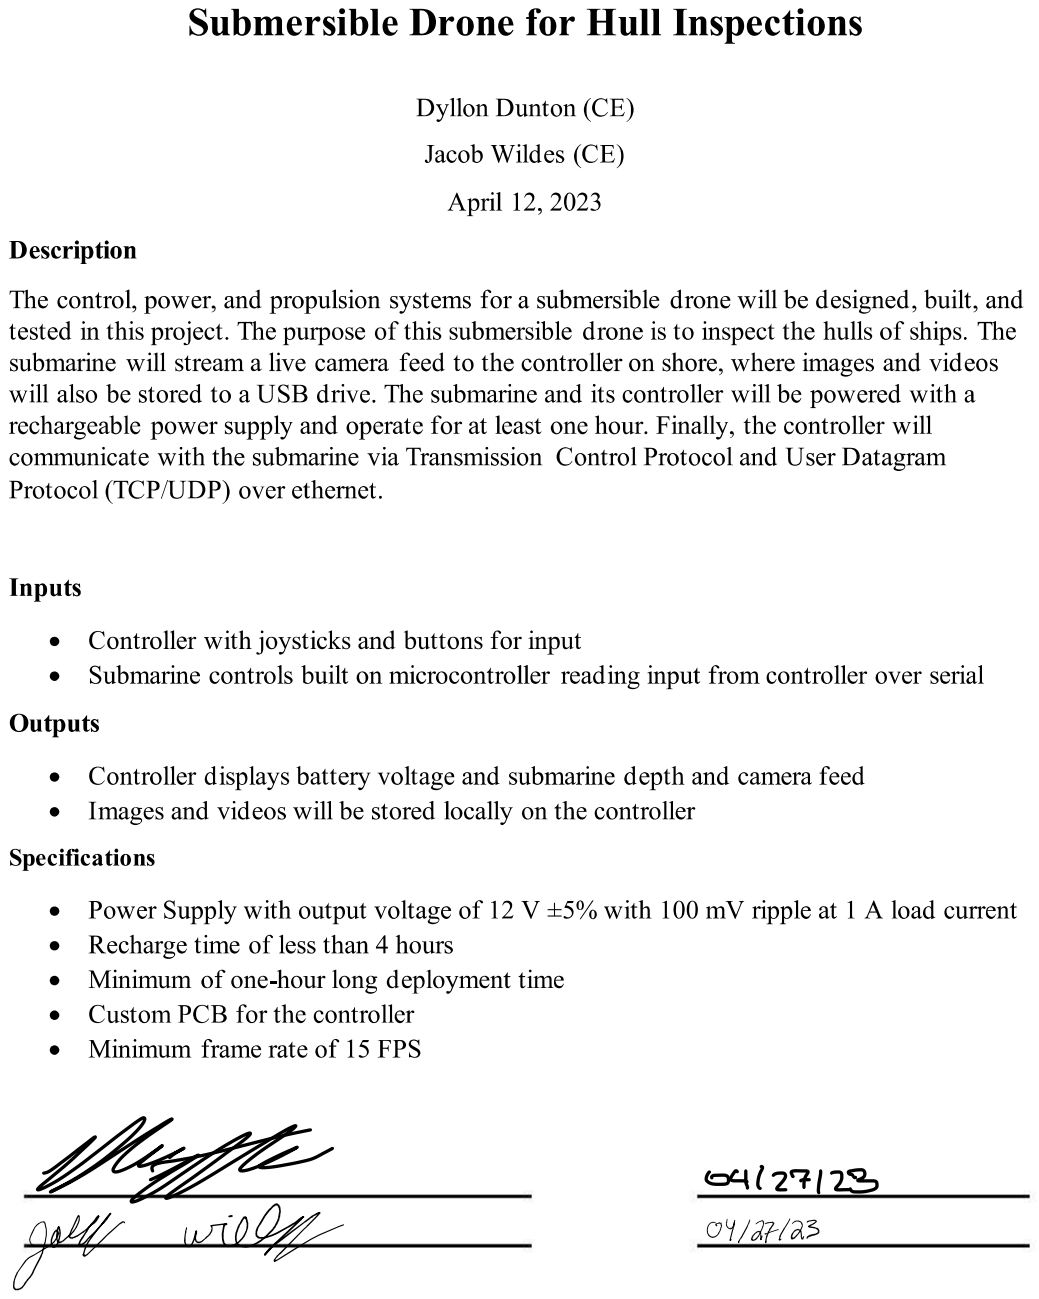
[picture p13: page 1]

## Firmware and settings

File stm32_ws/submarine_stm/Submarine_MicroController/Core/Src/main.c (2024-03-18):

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
/* Includes ------------------------------------------------------------------*/
#include "main.h"

/* USER CODE BEGIN Includes */
#include "string.h"
#include "math.h"
#include "stdio.h"

#include "perception.h"
#include "planner.h"
#include "controller.h"
#include "actuator.h"
/* USER CODE END Includes */

ADC_HandleTypeDef hadc1;
DMA_HandleTypeDef hdma_adc1;

I2C_HandleTypeDef hi2c1;

UART_HandleTypeDef hlpuart1;
UART_HandleTypeDef huart3;

TIM_HandleTypeDef htim3;
TIM_HandleTypeDef htim4;
TIM_HandleTypeDef htim5;

PCD_HandleTypeDef hpcd_USB_OTG_FS;

void SystemClock_Config(void);
static void MX_GPIO_Init(void);
static void MX_DMA_Init(void);
static void MX_ADC1_Init(void);
static void MX_I2C1_Init(void);
static void MX_LPUART1_UART_Init(void);
static void MX_USART3_UART_Init(void);
static void MX_USB_OTG_FS_PCD_Init(void);
static void MX_TIM3_Init(void);
static void MX_TIM4_Init(void);
static void MX_TIM5_Init(void);
/* USER CODE BEGIN 0 */
volatile uint8_t rx_received = 0;
volatile uint8_t rx_data[42];
char tx_buffer[100];
uint32_t adcs[3];



/* USER CODE END 0 */

/**
  * @brief  The application entry point.
  * @retval int
  */
int main(void)
{
  /* MCU Configuration--------------------------------------------------------*/

  /* Reset of all peripherals, Initializes the Flash interface and the Systick. */
  HAL_Init();

  /* Configure the system clock */
  SystemClock_Config();

  /* Initialize all configured peripherals */
  MX_GPIO_Init();
  MX_DMA_Init();
  MX_ADC1_Init();
  MX_I2C1_Init();
  MX_LPUART1_UART_Init();
  MX_USART3_UART_Init();
  MX_USB_OTG_FS_PCD_Init();
  MX_TIM3_Init();
  MX_TIM4_Init();
  MX_TIM5_Init();
  /* USER CODE BEGIN 2 */
	MTR_DRV_INIT();
	HAL_UART_Receive_IT(&hlpuart1, (uint8_t *)rx_data, 42); //Init recieve global interupt for 35 bit buffer
	HAL_TIM_PWM_Start(&htim3, TIM_CHANNEL_2);
	HAL_TIM_PWM_Start(&htim3, TIM_CHANNEL_3);
	HAL_TIM_PWM_Start(&htim4, TIM_CHANNEL_3);
	HAL_TIM_PWM_Start(&htim4, TIM_CHANNEL_4);
	HAL_TIM_PWM_Start(&htim5, TIM_CHANNEL_2);
	HAL_TIM_PWM_Start(&htim5, TIM_CHANNEL_3);
	
  /* USER CODE END 2 */

  /* Infinite loop */
  /* USER CODE BEGIN WHILE */
  while (1)
  {
  	
	if (rx_received) //New Transmission from RPI
	{
		HAL_ADC_Start_DMA(&hadc1, adcs, 3); //Grab ADC values
		struct envData inputs = envRead(adcs); //Store ADCs and inputs
		struct goalCommand command = parseComs(rx_data); //Get serial data and store command
		struct actuator_command control = controller(command, inputs); //use sensor data and command to set controls
		updateActuators(hlpuart1, control); //Set motors and transmit data back to Raspberry Pi
		
		rx_received = 0; //get ready for next transmission
	}
		

  	
  	
    /* USER CODE END WHILE */

    /* USER CODE BEGIN 3 */
  }
  /* USER CODE END 3 */
}

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
/* USER CODE BEGIN 4 */
void HAL_UART_RxCpltCallback(UART_HandleTypeDef *huart)
{
	//UNUSED(huart); //waring suppresion
	
	//HAL_GPIO_TogglePin(GPIOB, GPIO_PIN_14); //toggle LED for dev
	rx_received = 1;//set flag for use in while loop
	
	HAL_UART_Receive_IT(&hlpuart1, (uint8_t *)rx_data, 42); //reset UART interupt for next transmission
}





/* USER CODE END 4 */
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


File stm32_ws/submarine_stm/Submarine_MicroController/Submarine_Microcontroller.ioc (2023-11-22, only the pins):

Mcu.UserName=STM32L4R5ZITx
PA0.Signal=ADCx_IN5
PA10.GPIO_Label=USB_ID
PA10.Signal=USB_OTG_FS_ID
PA11.GPIO_Label=USB_DM
PA11.Signal=USB_OTG_FS_DM
PA12.GPIO_Label=USB_DP
PA12.Signal=USB_OTG_FS_DP
PA3.Signal=GPIO_Output
PA4.Signal=GPIO_Output
PA5.Signal=GPIO_Output
PA6.Signal=GPIO_Output
PA7.Signal=GPIO_Output
PA8.GPIO_Label=USB_SOF [TP1]
PA8.Signal=USB_OTG_FS_SOF
PA9.GPIO_Label=USB_VBUS
PA9.Signal=USB_OTG_FS_VBUS
PB0.Signal=GPIO_Output
PB1.Signal=GPIO_Output
PB14.GPIO_Label=LD3 [Red]
PB14.Signal=GPIO_Output
PB2.Signal=GPIO_Output
PB7.GPIO_Label=LD2 [Blue]
PB7.Signal=GPIO_Output
PB8.Signal=I2C1_SCL
PB9.Signal=I2C1_SDA
PC0.Signal=ADCx_IN1
PC1.Signal=ADCx_IN2
PC13.GPIO_Label=B1
PC13.Signal=GPXTI13
PC3.Signal=ADCx_IN4
PC4.Signal=GPIO_Output
PC5.Signal=GPIO_Output
PD14.Signal=S_TIM4_CH3
PD15.Signal=S_TIM4_CH4
PD8.GPIO_Label=STLK_RX [STM32F103CBT6_PA3]
PD8.Signal=USART3_TX
PD9.GPIO_Label=STLK_TX [STM32F103CBT6_PA2]
PD9.Signal=USART3_RX
PE10.Signal=GPIO_Input
PE11.Signal=GPIO_Input
PE12.Signal=GPIO_Input
PE13.Signal=GPIO_Input
PE4.Signal=S_TIM3_CH2
PE5.Signal=S_TIM3_CH3
PE7.Signal=GPIO_Output
PE8.Signal=GPIO_Output
PE9.Signal=GPIO_Output
PF12.Signal=GPIO_Output
PF13.Signal=GPIO_Output
PF14.Signal=GPIO_Output
PF15.Signal=GPIO_Output
PF7.Signal=S_TIM5_CH2
PF8.Signal=S_TIM5_CH3
PG0.Signal=GPIO_Output
PG1.Signal=GPIO_Output
PG5.GPIO_Label=USB_OverCurrent [STMPS2151STR_FAULT]
PG5.Signal=GPIO_Input
PG6.GPIO_Label=USB_PowerSwitchOn [STMPS2151STR_EN]
PG6.Signal=GPIO_Output
PG7.GPIO_Label=STLINK_TX
PG7.Signal=LPUART1_TX
PG8.GPIO_Label=STLINK_RX
PG8.Signal=LPUART1_RX

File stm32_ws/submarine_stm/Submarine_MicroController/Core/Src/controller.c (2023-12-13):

#include "controller.h"
#define ADC_RECORD_COUNT 10
#define WAIT_COUNT 2

/*
Dyllon Dunton
12/11/2023

This file uses the sensor data and the command from the controller to set values for
driving the motors
*/

//Step values for motors
uint8_t steps[4] = {0b1010, 0b0110, 0b0101, 0b1001};

//current step that the motors are on
int current_left = 0;
int current_right = 0;

//Timer value for the 
int counter = 0;


struct actuator_command controller(struct goalCommand com_data, struct envData in)
{
	//DO PID controller
	struct actuator_command actuate;
	
	actuate.in = in;
	actuate.com = com_data;
	propellor_control(&actuate);
	servo_control(&actuate);
	stepper_control(&actuate);
	
	return actuate;
}

void propellor_control(struct actuator_command *act)
{
	float leftThrust;
	float rightThrust;
	float forThrust;
	float backThrust;
	
	//Convert coms thrust vals in percentages for f,b,l,r
  if (act->com.turnThrust < 128) 
  {
  	leftThrust = ((float)(-act->com.turnThrust + 128))/256.0; // 0% <. 50% 
  	rightThrust = 0;
  }
  else
  {
  	leftThrust = 0;
  	rightThrust = ((float)(act->com.turnThrust - 128))/256.0; // 0% <. 50% 
  }
  
  if (act->com.forwardThrust < 128)
  {
  	forThrust = 0;
		backThrust = ((float)(-act->com.forwardThrust + 128))/256.0; // 0% <. 50%
  }
  else
  {
  	forThrust = ((float)(act->com.forwardThrust - 128))/256.0; // 0% <. 50%
		backThrust = 0;
  }
  
  //mix individual thrust values into 
  act->rightPropThrust = leftThrust - rightThrust + forThrust - backThrust; // -100% <. 100%
  act->leftPropThrust = rightThrust - leftThrust + forThrust - backThrust; // -100% <. 100%
}

void servo_control(struct actuator_command *act)
{
	//Setup for 0.5ms <. 2.5ms
  act->camVerticalDuty = (0.000392 * (float)act->com.camUpDown) + 0.025;
  act->camHorizontalDuty = (0.000392 * (float)act->com.camLeftRight) + 0.025;
}

void stepper_control(struct actuator_command *act)
{
	counter++;
	if (counter >= WAIT_COUNT)
	{
		counter = 0;
		HAL_GPIO_TogglePin(GPIOB, GPIO_PIN_14); //toggle LED for dev
		
		//take in the roll value from the submarine
		int roll = ((int)(act->com.roll)) - 90; // -90 <. 90
		int cw = 0;
		
		//calc clockwise steps to be proportional to the roll with a max of 30  
		if (roll > 0) cw = fmin(roll, 30);
		else cw = fmax(roll, -30);
		
		//Split into left and right
		int left = cw; 
		int right = -cw;
		
		//add on depth
		if (act->com.depthUp) 
		{
			left += 15;
			right += 15;
		}
		else if (act->com.depthDown)
		{
			left -= 15;
			right -= 15;
		}
		
		//turn to adc value
		//convert [-45,45] to [30, 225]
		int left_adc = (196*left)/90 + 128;
		int right_adc = (196*right)/90 + 128;
		
		//turn into step values
		if (left_adc < act->in.adc.leftBallastPosition)
		{	
			//left down
			current_left--;
			if (current_left == -1) current_left = 3;
		}
		
		else if (left_adc > act->in.adc.leftBallastPosition)
		{	
			//left up
			current_left++;
			if (current_left == 4) current_left = 0;
		}
		
		if (right_adc < act->in.adc.rightBallastPosition)
		{	
			//right down
			current_right--;
			if (current_right == -1) current_right = 3;
		}
		else if (right_adc > act->in.adc.rightBallastPosition)
		{	
			//right up
			current_right++;
			if (current_right == 4) current_right = 0;
		}
	}
	
	//create structs to hold current steps to send to the controller
	act->left_current = current_left;
	act->right_current = current_right;
	
	//Create structs to hold step values to send to the drivers
	struct stepper_instruction leftStep;
	struct stepper_instruction rightStep;
	
	//Parse out the steps for each lead of each motor
	leftStep.a_one = steps[current_left] & 0b1000;
	leftStep.a_two = steps[current_left] & 0b0100;
	leftStep.b_one = steps[current_left] & 0b0010;
	leftStep.b_two = steps[current_left] & 0b0001;
	
	rightStep.a_one = steps[current_right] & 0b1000;
	rightStep.a_two = steps[current_right] & 0b0100;
	rightStep.b_one = steps[current_right] & 0b0010;
	rightStep.b_two = steps[current_right] & 0b0001;
	
	act->left_stepper = leftStep;
	act->right_stepper = rightStep;
	
}

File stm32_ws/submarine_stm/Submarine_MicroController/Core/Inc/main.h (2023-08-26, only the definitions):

#define B1_Pin GPIO_PIN_13
#define B1_GPIO_Port GPIOC
#define LD3_Pin GPIO_PIN_14
#define LD3_GPIO_Port GPIOB
#define STLK_RX_Pin GPIO_PIN_8
#define STLK_RX_GPIO_Port GPIOD
#define STLK_TX_Pin GPIO_PIN_9
#define STLK_TX_GPIO_Port GPIOD
#define USB_OverCurrent_Pin GPIO_PIN_5
#define USB_OverCurrent_GPIO_Port GPIOG
#define USB_PowerSwitchOn_Pin GPIO_PIN_6
#define USB_PowerSwitchOn_GPIO_Port GPIOG
#define STLINK_TX_Pin GPIO_PIN_7
#define STLINK_TX_GPIO_Port GPIOG
#define STLINK_RX_Pin GPIO_PIN_8
#define STLINK_RX_GPIO_Port GPIOG
#define USB_SOF_Pin GPIO_PIN_8
#define USB_SOF_GPIO_Port GPIOA
#define USB_VBUS_Pin GPIO_PIN_9
#define USB_VBUS_GPIO_Port GPIOA
#define USB_ID_Pin GPIO_PIN_10
#define USB_ID_GPIO_Port GPIOA
#define USB_DM_Pin GPIO_PIN_11
#define USB_DM_GPIO_Port GPIOA
#define USB_DP_Pin GPIO_PIN_12
#define USB_DP_GPIO_Port GPIOA
#define TMS_Pin GPIO_PIN_13
#define TMS_GPIO_Port GPIOA
#define TCK_Pin GPIO_PIN_14
#define TCK_GPIO_Port GPIOA
#define SWO_Pin GPIO_PIN_3
#define SWO_GPIO_Port GPIOB
#define LD2_Pin GPIO_PIN_7
#define LD2_GPIO_Port GPIOB

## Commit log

2023-07-26 Added framework for our code
2023-07-27 Added a couple dependencies to controller GUI, not yet functioning
2023-07-27 Fixed ament build, currently having subscription trouble
    [con_gui.py, con_pub.py]
2023-07-28 Fixed ROS1 and 2 type error, debugging downstream errors
    [con_gui.py]
2023-08-14 Rearranged pinout on controller STM board
2023-08-15 Ready to test serial between stm32 sub and pi
2023-08-16 Fix baud rate of LPUART
    [Submarine_Microcontroller.ioc, main.c]
2023-08-16 Add in toggle LED to test board function
2023-08-16 Final fix to merge issue
    [main.c]
2023-08-16 Switch to USART3
2023-08-16 Try to fix USART3 for stlink us coms
    [Submarine_Microcontroller.ioc]
2023-08-18 ADC is polling how I want, need to clean up debug and transmit on UART
2023-08-24 Controller UART working the way we want
2023-08-24 Create new serial test for recieve (Forgot to enable global interupt for uart
2023-08-24 Working UART, need to do single bit decoding next
2023-08-25 First attempt at getting i2C to work with the IMU (FAIL)
    [i2c_serialtest.py, main.c]
2023-08-25 Added a base docker image - needs debug
    [controller_compose.yaml]
2023-08-25 Ready for i2c help from sheaff and ros working? on sub
2023-08-26 Add setup for motor init
2023-08-26 Add TIM3 CH2,3 for propellor pwms at 10khz
2023-08-26 write code for propellor pwm, need to set up rest of pwm for prop and servo
2023-08-26 Finish init of all pwm timers
2023-08-26 Add Duty Cycle test, need to test in IDE because UART not working as expected
    [dcTest.py, main.c]
2023-08-27 Working Propellor code (Test with Oscope)
2023-08-27 Set up servo timers
2023-08-27 Servos working
2023-08-27 Fix ros on sub to fix bitfield to pad 0s
    [main.c, sub_coms.py]
2023-08-27 Docker image for controller builds - debugging device attachment and GUI
    [controller_compose.yaml, publish_controller.yaml]
2023-08-27 Serial connects and broadcasts as should, need to fix GUI
    [controller_compose.yaml]
2023-08-27 Began stepper updating, need to do more work to figure out stepper architecture
2023-08-27 Docker GUI works
    [controller_compose.yaml]
2023-08-30 Add manufacturing STLs
    [BackCap.stl, Balast_Left.stl, Balast_Right.stl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]
2023-08-30 Add Printing README
2023-08-30 Create README.md for stm32_ws
2023-09-04 Added a battery percentage monitor as a testbench
2023-09-05 Everything split apart but uart receive no longer works
    [actuator.c, biserialtest.py, controller.c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]
2023-09-05 Regenerate to maybe fix uart issues
2023-09-05 Rearrange the layout and make battery prettier
2023-09-06 I2C working
2023-09-21 GUI partially works in the ROS workspace. Needs to tidying up. Need to verify the framerate:
2023-09-21 Battery bar and ballasts show nicely in the end function
2023-10-30 Finish state estimation, need to finish stepper control and fix uart i2c and adc
    [actuator.c, controller.c]
2023-10-31 Almost done with stepper control. Need to do a couple of things
2023-11-01 Finally done logic for stepper controller
2023-11-06 Decided to axe normalization, didn't mesh with Dyllon's subside
    [con_pub.py]
2023-11-06 Controls coded up trying to fix uart
    [actuator.c, controller.c, main.c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]
2023-11-06 Maybe fixed uart?
2023-11-19 upload most recent code before moving back to fix uart
    [actuator.c, controller.c, dcTest.py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]
2023-11-20 Add test for imu so jacob can test
2023-11-20 Added an error cr check to file to make sure that the IMU stays querying even if the stream is temporarily interrupted
2023-11-20 Possibly added IMU function to ros network
2023-11-20 Clarity in comments in ROS2 IMU
2023-11-22 Fixed syntax errors in overlay
    [overlay.py]
2023-11-22 Fixed problems, made problems
    [con_gui.py, con_pub.py]
2023-11-24 Jacob has added many systemd files and is very tired :/
2023-11-25 Beginning to try and fix FPS issue
    [con_gui.py]
2023-11-25 Verified that camera hardware is at fault. Need better USB camera
2023-12-03 Add pcb files
    [DualDriver.SchDoc, DualDriverProp.SchDoc, DualDriverStepperLeft.SchDoc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]
2023-12-10 Added final GUI fixes (battery no longer displays incorrectly, ballasts accurate
    [con_gui.py, con_pub.py, overlay.py]
2023-12-10 Made fixes so that the stepper motors spin properly and respond to roll inputs
    [Submarine_Microcontroller.ioc, actuator.c, controller.c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]
2023-12-12 Need to remake the pcbfiles since I accidentally deleted them :(
    [DualDriverProp.SchDoc, DualDriverStepperLeft.SchDoc, DualDriverStepperRight.SchDoc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]
2023-12-12 Update Schematic
    [DualDriverProp.SchDoc, DualDriverStepperLeft.SchDoc, DualDriverStepperRight.SchDoc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]
2023-12-13 Fix issues after recommenting
    [controller.c, sub_coms.py]
2024-02-25 Update controller main.c with where the adc is init

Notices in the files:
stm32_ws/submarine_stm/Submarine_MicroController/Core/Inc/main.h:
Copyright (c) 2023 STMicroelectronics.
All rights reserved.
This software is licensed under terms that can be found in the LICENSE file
